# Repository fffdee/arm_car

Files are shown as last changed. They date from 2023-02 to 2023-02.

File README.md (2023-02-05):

# arm_car铁甲虫遥控小车

### 关于模型（model）

#### 1.除了电机，轴承还有轮子不用打印，其他都可以用3d打印。

#### 2.准备标准件：轴承（10mm*3mm）x4，螺钉（20mm以上*3mm）x4，舵机x2，N20电机（长轴:大于12mm）x2，N20电机轮子x2

### 关于软件（software）

#### 1.只需要修改wifi或者手机热点的名称和密码即可

### 关于硬件（hardware）

#### geber 文件夹下是打板文件

#### BOM 文件夹下是零件清单（SMT用）

#### pick 文件下是坐标文件（SMT用）

### 关于APP

#### 打开后输入192.168.190.125（小车ip，可以在软件中修改）就可开始控制小车了（保证小车已经连上wifi或者手机热点）

#### 视频详情链接：【【开源】寒假在家无聊，做了一个甲虫车】 https://www.bilibili.com/video/BV1HY411D7DA/?share_source=copy_web&vd_source=6f5872d400f2b982828888d93e5dddf6

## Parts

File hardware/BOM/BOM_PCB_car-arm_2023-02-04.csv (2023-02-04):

ID | Name | Designator | Footprint | Quantity | Manufacturer Part | Manufacturer | Supplier | Supplier Part | Price
1 | LESD8D3.3CAT5G | D3,D4 | SOD-882_L1.0-W0.6-BI | 2 | LESD8D3.3CAT5G | LRC(乐山无线电) | LCSC | C172409 | 0.0894
2 | HDR-M-2.54_1x2 | J5,J6,J1 | HDR-M-2.54_1X2 | 3 |  |  | LCSC | C124375 | 0.1611
3 | 10u | C1,C2,C6,C12,C13,C14,C18,C22 | C0402 | 8
4 | 0.1u | C3,C4,C5,C8,C9,C10,C11,C17,C20,C21,C26 | C0402 | 11
5 | 22pf | C7 | C0402 | 1
6 | 10U | C15,C16 | C0402 | 2
7 | 1u | C19 | C0402 | 1
8 | LESD5D5.0CT1G | D2 | SOD-523_L1.2-W0.8-LS1.6-BI | 1 | LESD5D5.0CT1G | LRC(乐山无线电) | LCSC | C383211 | 0.1559
9 | SS-12D00-G4 | NO-> | SS-12D00-G4 | 1
10 | HDR-M-2.54_1x3 | J2,J3,J4 | HDR-M-2.54_1X3 | 3 |  |  | LCSC | C180248 | 1.2443
11 | 2.2uH | L6 | IND-SMD_L3.5-W3.0 | 1 | SMTDR32-2R2M | 3L COILS | LCSC | C326182 | 0.6574
12 | LED-0603_G | LED4 | LED0603_GREEN | 1 | 19-217/GHC-YR1S2/3T | EVERLIGHT(台湾亿光) | LCSC | C72043 | 0.1678
13 | LED-0603_R | LED5 | LED0603_RED | 1 | 19-217/R6C-AL1M2VY/3T | EVERLIGHT(台湾亿光) | LCSC | C72044 | 0.1041
14 | AO3401A | Q1 | SOT-23_L2.9-W1.3-P1.90-LS2.4-BR | 1 | AO3401A | AOS | LCSC | C15127 | 0.5469
15 | S8050 | Q2,Q3 | SOT-23(SOT-23-3) | 2 | S8050 | Yenji | LCSC | C364312 | 0.0687
16 | 100k | R1,R2,R5,R8 | R0402 | 4
17 | 1k | R6,R7,R9,R10 | R0402 | 4
18 | 10k | R18,R19,R23,R24,R25,R26,R27,R47 | R0402 | 8
19 | 1.2K | R28 | R0402 | 1
20 | 0 | R29 | R0402 | 1
21 | 580k | R48 | R0402 | 1
22 | 150k | R49 | R0402 | 1
23 | sw1 | SW1,SW2 | 3*4龟仔按键 | 2 | TS-1101-C-W | XKB Connectivity(中国星坤) | LCSC | C318938 | 0.2205
24 | RZ7888 | U1,U2 | SOP-8_L4.9-W3.9-P1.27-LS6.0-BL | 2 | RZ7888 | RZ | LCSC | C94177 | 2.1132
25 | SY8088AAC | U3 | SOT-23-5_L3.0-W1.7-P0.95-LS2.8-BR | 1 | SY8088AAC | Silergy | LCSC | C79313 | 0.5151
26 | ME6211C33M5G | U4 | SOT-23-5_L3.0-W1.7-P0.95-LS2.8-BR | 1 | ME6211C28M5G-N | MICRONE(南京微盟) | LCSC | C53099 | 0.4775
27 | W2812B | U5,U6,U7,U8 | LED-SMD_4P-L5.0-W5.0-LS5.4-TL | 4 | W2812B | null | LCSC | C2935753
28 | TP4056 | U11 | ESOP-8_L4.9-W3.9-P1.27-LS6.0-BL-EP | 1 | TP4056 | TOPPOWER | LCSC | C16581 | 1.2281
29 | ESP-12F(ESP8266MOD) | U12 | WIFIM-SMD_ESP-12F-ESP8266MOD | 1 | ESP-12F(ESP8266MOD) | Ai-Thinker | LCSC | C82891 | 13.51
30 | CH340C | U13 | SOP-16_150MIL | 1 | CH340C | WCH | LCSC | C84681 | 3.01
31 | TYPEC-304J-BCP16 | USB1 | USB-C-SMD_TYPEC-304J-BCP16 | 1 | TYPEC-304J-BCP16 | XUNPU(讯普) | LCSC | C2835315 | 2.25

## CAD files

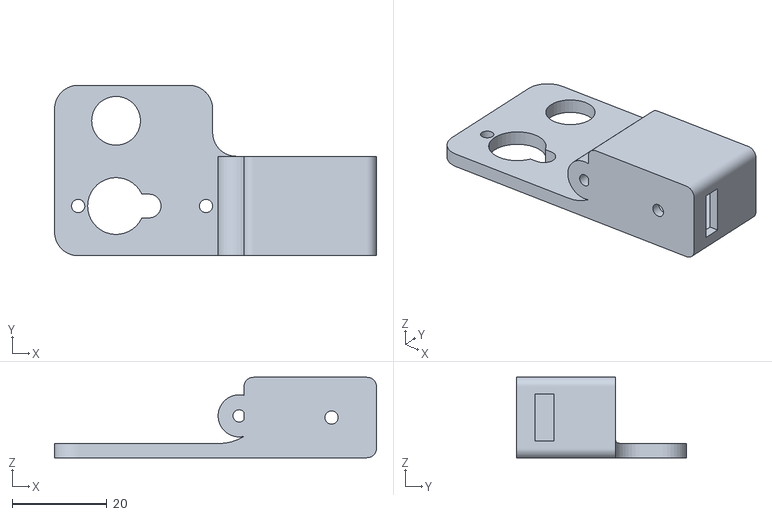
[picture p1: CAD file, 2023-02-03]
model/STL/动力臂.STL
68.0 x 36.0 x 17.0

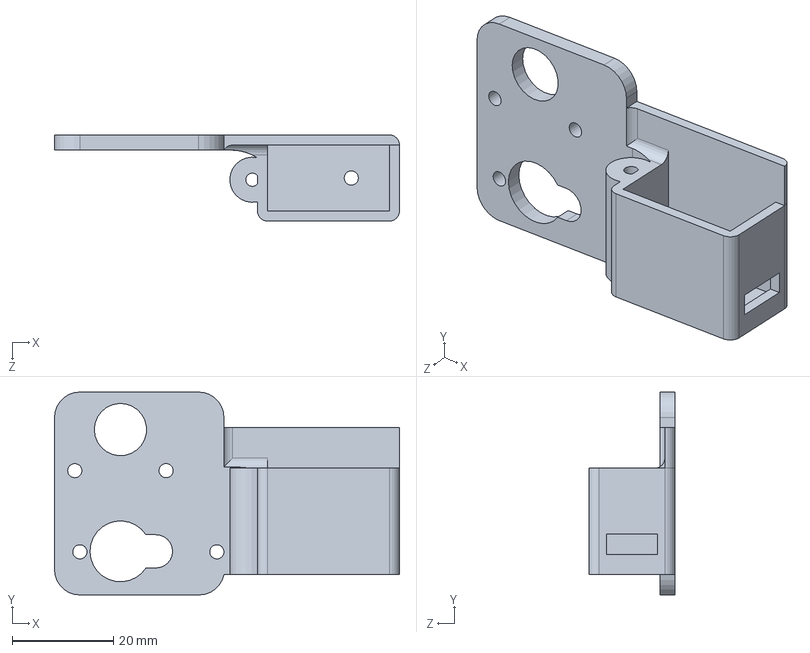
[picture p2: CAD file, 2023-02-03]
model/云台.SLDPRT
68.0 x 40.0 x 17.0 mm

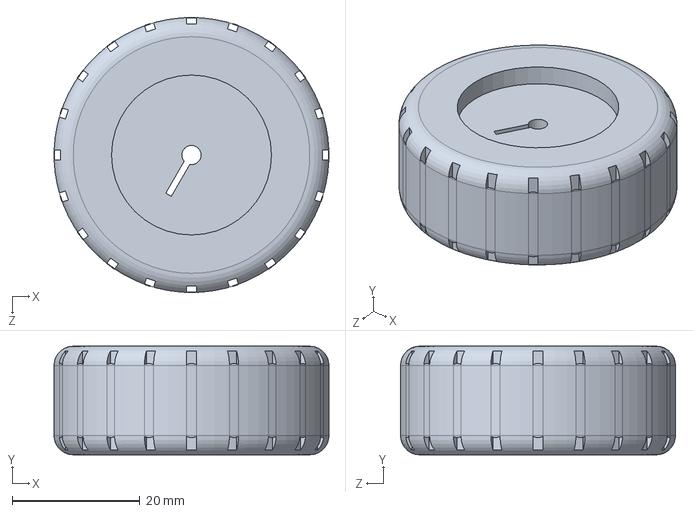
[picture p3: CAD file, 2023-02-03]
model/轮子.SLDPRT
43.0 x 17.0 x 43.0 mm

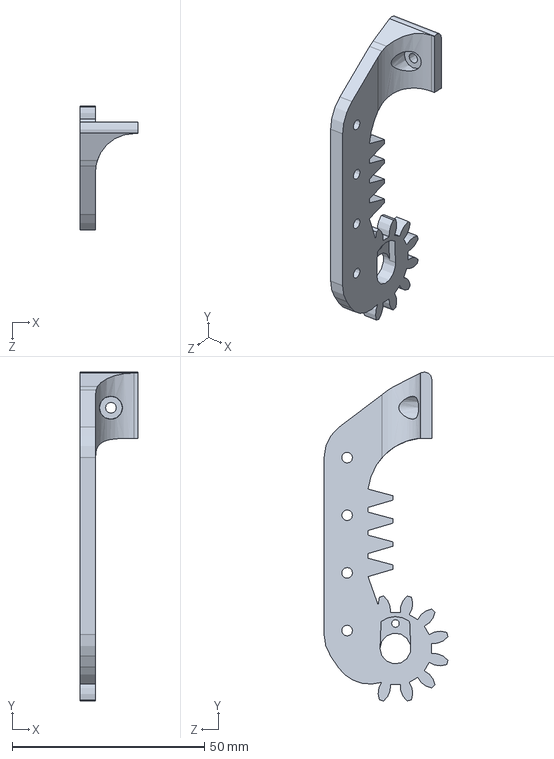
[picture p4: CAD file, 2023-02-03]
model/动力齿轮.SLDPRT
15.0 x 85.6 x 32.2 mm

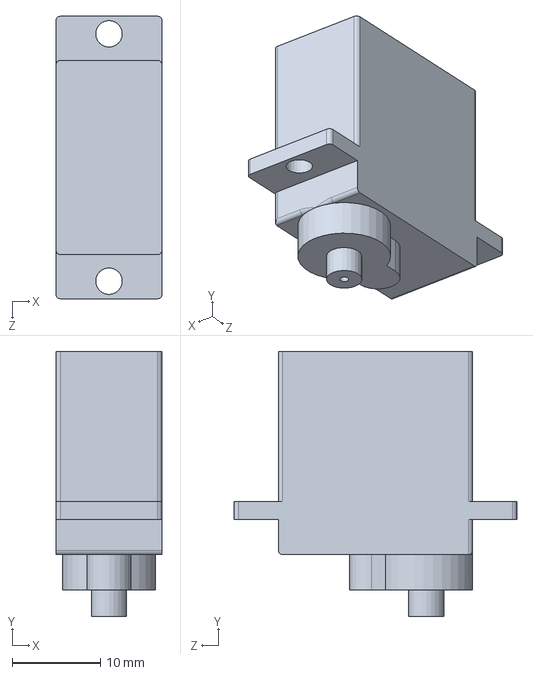
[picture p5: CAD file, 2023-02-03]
model/蓝色小舵机.SLDPRT
12.0 x 30.0 x 32.0 mm

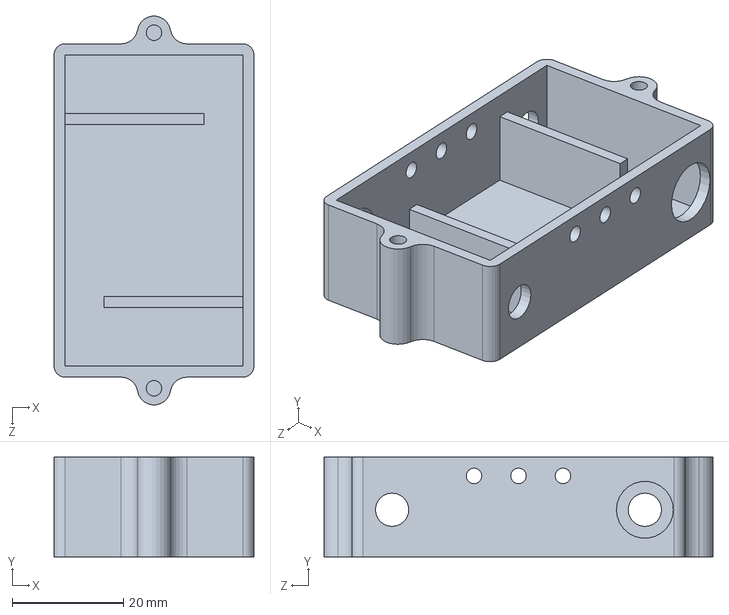
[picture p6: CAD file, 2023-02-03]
model/底盘.SLDPRT
36.0 x 18.0 x 70.0 mm

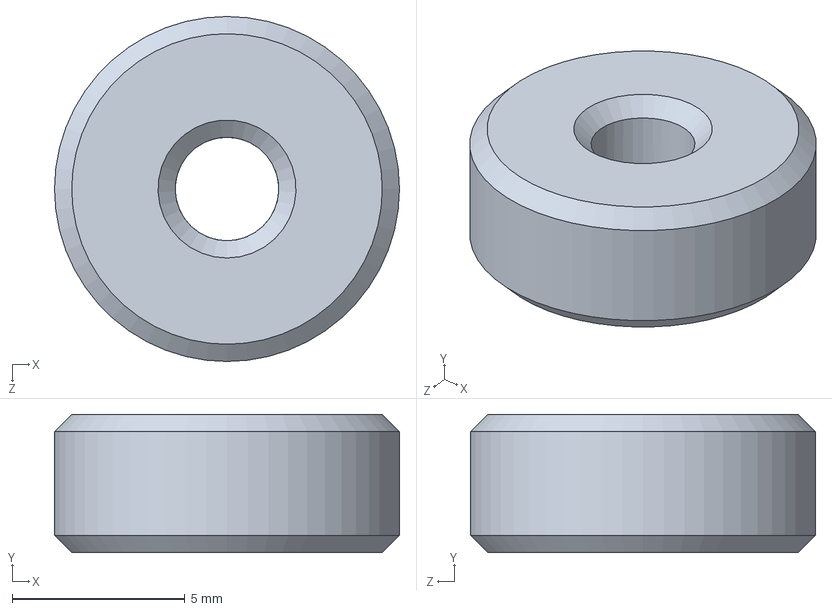
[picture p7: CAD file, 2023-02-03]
model/轴承.SLDPRT
10.0 x 4.00 x 10.0 mm

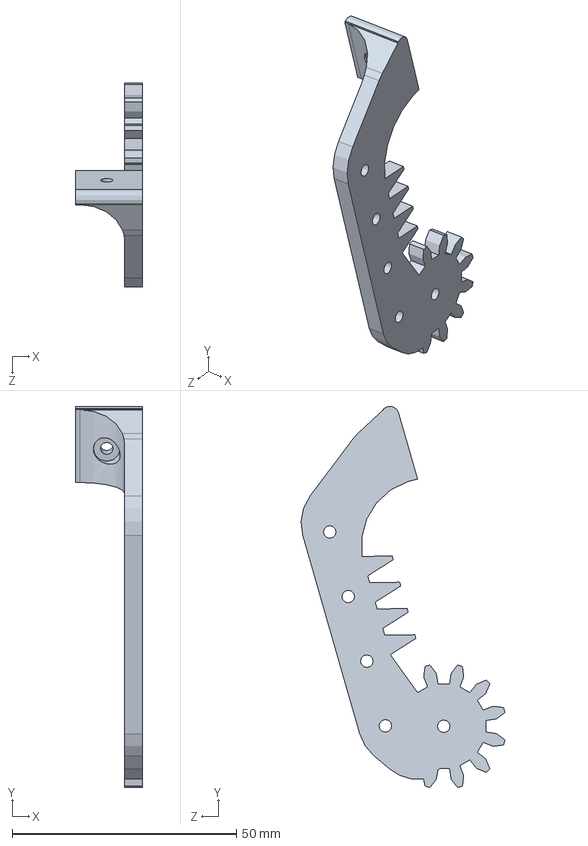
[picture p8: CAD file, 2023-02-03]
model/辅助齿轮齿轮.SLDPRT
15.0 x 85.0 x 45.5 mm

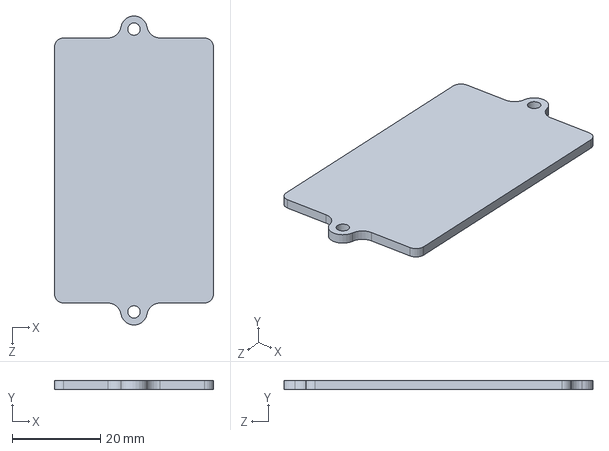
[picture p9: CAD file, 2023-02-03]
model/盖板.SLDPRT
36.0 x 2.00 x 70.0 mm

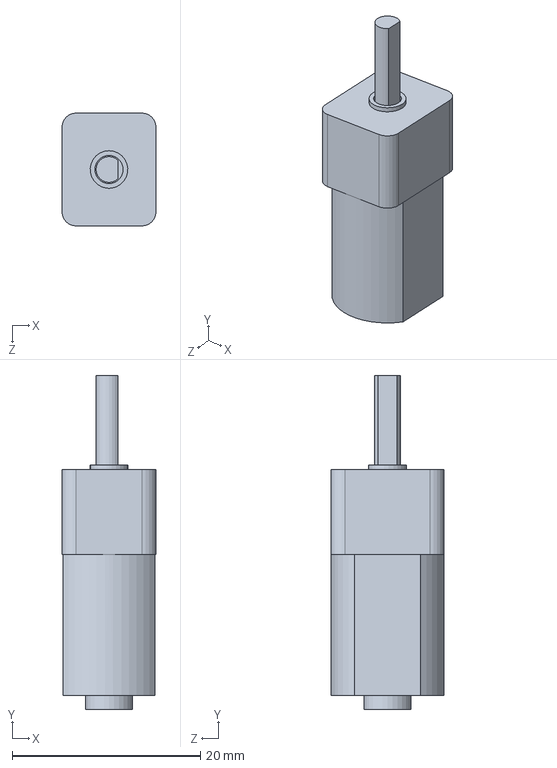
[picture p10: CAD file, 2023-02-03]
model/N20电机.SLDPRT
10.0 x 35.5 x 12.0 mm

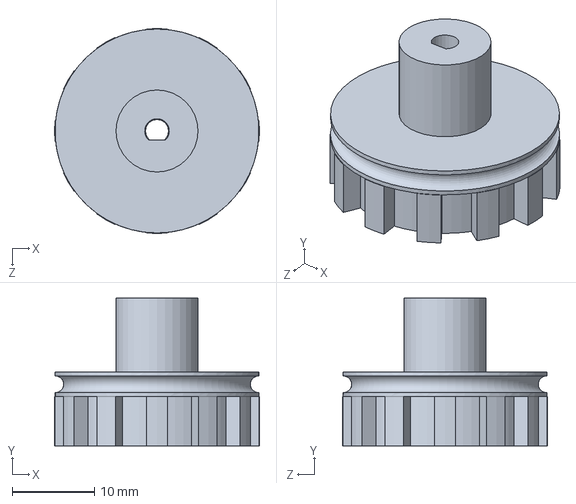
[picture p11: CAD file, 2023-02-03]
model/轮子连接器.SLDPRT
25.0 x 18.0 x 25.0 mm

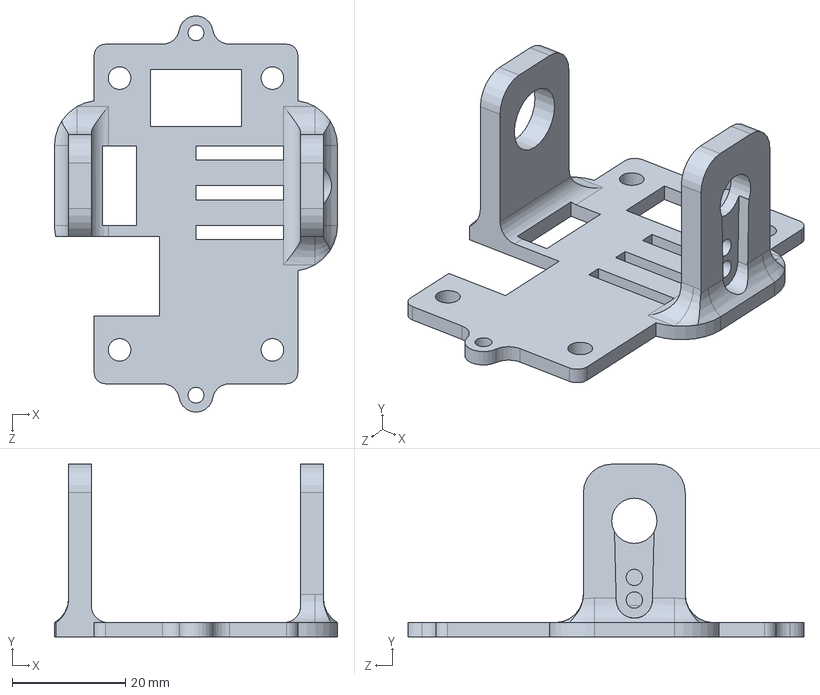
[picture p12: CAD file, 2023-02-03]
model/盖板舵机台.SLDPRT
50.0 x 30.5 x 70.0 mm

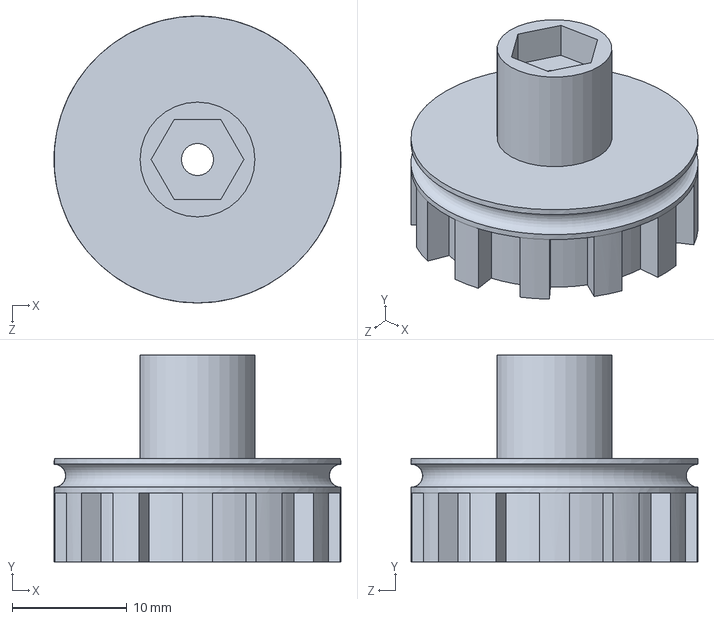
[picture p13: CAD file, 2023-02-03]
model/从动连接器 .SLDPRT
25.0 x 18.0 x 25.0 mm

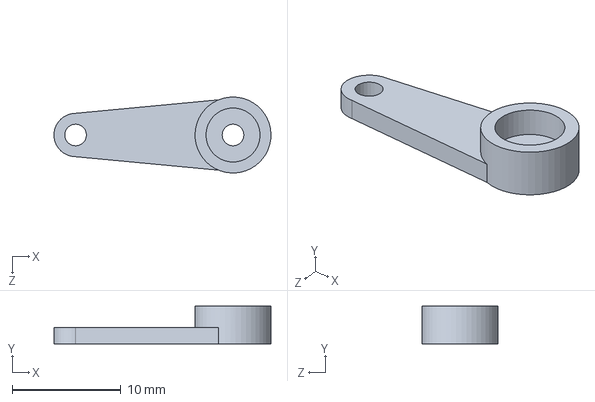
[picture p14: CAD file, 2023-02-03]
model/舵机柄.SLDPRT
20.0 x 3.50 x 7.00 mm

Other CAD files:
model/电池.SLDPRT
model/STL/云台.STL
model/STL/从动连接器 .STL
model/STL/动力齿轮.STL
model/STL/底盘.STL
model/STL/盖板舵机台.STL
model/STL/轮子连接器.STL
model/STL/辅助齿轮齿轮.STL

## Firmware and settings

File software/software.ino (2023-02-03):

 #include <ESP8266WiFi.h>
#include <ESP8266WiFiMulti.h>   // 使用WiFiMulti库 
#include <ESP8266WebServer.h>   // 使用WebServer库
#include <Servo.h> 
#include <EEPROM.h>
#include "StringSplitter.h"
#include <WiFiUdp.h>
#include <Adafruit_NeoPixel.h>

Servo myServo2;
Servo myServo1;

Adafruit_NeoPixel pixels(4, 5, NEO_GRB + NEO_KHZ800);


ESP8266WiFiMulti wifiMulti;     // 建立ESP8266WiFiMulti对象,对象名称是 'wifiMulti'
 
ESP8266WebServer server(80);    // 建立网络服务器对象，该对象用于响应HTTP请求。监听端口（80）
 
IPAddress local_IP(192, 168, 190, 125); // 设置开发板联网后的IP（这个就是填到app里面的IP地址）
IPAddress gateway(192, 168, 190, 1);    // 设置网关IP（通常网关IP是手机的IP）（开热点给开发板连的手机）
IPAddress subnet(255, 255, 255, 0);   // 设置子网掩码
IPAddress dns(192,168,190,1);           // 设置局域网DNS的IP（通常局域网DNS的IP是手机的IP）（开热点给开发板连的手机）

int servo1Value=90;
int servo2Value=90;

int speedValue=200;
int anglexValue = 90;
int angleyValue = 90;
void setup(void){
  
  Serial.begin(115200);          // 启动串口通讯
  EEPROM.begin(25);
  myServo2.attach(12); //设置引脚2为舵机引脚
  myServo1.attach(14);  
  myServo1.write(anglexValue);
  myServo2.write(angleyValue);
  pinMode(13,OUTPUT);
  pinMode(16,OUTPUT);
  pinMode(0,OUTPUT);
  pinMode(4,OUTPUT);
  // 设置开发板网络环境
  if (!WiFi.config(local_IP, gateway, subnet)) {

  } 
  
  wifiMulti.addAP("BanGO", "88888888"); // 将需要连接的一系列WiFi ID和密码输入这里
  wifiMulti.addAP("ssid_from_AP_2", "your_password_for_AP_2"); // ESP8266-NodeMCU再启动后会扫描当前网络
  wifiMulti.addAP("ssid_from_AP_3", "your_password_for_AP_3"); // 环境查找是否有这里列出的WiFi ID。如果有
                            // 则尝试使用此处存储的密码进行连接。
  
  // 尝试进行wifi连接。
  while (wifiMulti.run() != WL_CONNECTED) { 
    delay(250);

  }
 

 
  server.on("/control", handleUpdate);        // 处理服务器更新函数
  server.on("/arm", arm);        // 处理服务器更新函数
  server.on("/hand", hand);        // 处理服务器更新函数
  server.on("/speed", Setspeed);
  server.begin();                            // 启动网站服务

  pixels.begin(); 
  pixels.clear();

  pixels.setPixelColor(0, pixels.Color(10,10,10));
  pixels.setPixelColor(1, pixels.Color(10,10,10));
  pixels.setPixelColor(2, pixels.Color(10,10,10));
  pixels.setPixelColor(3, pixels.Color(10,10,10));
  pixels.show();   // Send the updated pixel colors to the hardware.
  delay(1000);
  pixels.setPixelColor(0, pixels.Color(0,0,0));
  pixels.setPixelColor(1, pixels.Color(0,0,0));
  pixels.setPixelColor(2, pixels.Color(0,0,0));
  pixels.setPixelColor(3, pixels.Color(0,0,0));
  pixels.show();   // Send the updated pixel colors to the hardware.
  delay(1000);
}
 
void loop(void){
  server.handleClient(); // 检查http服务器访问


  delay(100);
}



//重点改这里就好了 
void arm(){
   anglexValue = server.arg("anglex").toInt(); 
   myServo1.write(anglexValue); 
   Serial.print("anglexValue = ");  Serial.println(anglexValue);
}

void hand(){
   angleyValue = server.arg("angley").toInt(); 
   myServo2.write(angleyValue); 
   Serial.print("angleyValue = ");  Serial.println(angleyValue);
}

void Setspeed(){
   speedValue = server.arg("speed").toInt(); 
  
   Serial.print("speedValue = ");  Serial.println(speedValue);
}

void handleUpdate(){
        // 获取客户端发送HTTP信息中的整数数值
  int leftupValue = server.arg("leftup").toInt();  // 获取客户端发送HTTP信息中的按键控制量
  int leftdownValue = server.arg("leftdown").toInt(); 
  int rightupValue = server.arg("right").toInt();
  int rightdownValue = server.arg("rightdown").toInt();
  int stopValue = server.arg("stop").toInt();              

 

  if(leftupValue == 1){
    analogWrite(0,speedValue);
    analogWrite(4,0);
   
    pixels.setPixelColor(0, pixels.Color(10,10,150));
    pixels.setPixelColor(1, pixels.Color(10,10,150));
    pixels.setPixelColor(2, pixels.Color(10,10,150));
    pixels.setPixelColor(3, pixels.Color(10,10,150));
    pixels.show();   // Send the updated pixel colors to the hardware.
 
   }

  if(leftdownValue == 1){

    analogWrite(0,0);
    analogWrite(4,speedValue);
    pixels.setPixelColor(0, pixels.Color(10,150,10));
    pixels.setPixelColor(1, pixels.Color(10,150,10));
    pixels.setPixelColor(2, pixels.Color(10,150,10));
    pixels.setPixelColor(3, pixels.Color(10,150,10));
    pixels.show();   // Send the updated pixel colors to the hardware.
  
  }
  if(stopValue == 1){
    analogWrite(13,0);
    analogWrite(16,0);
    analogWrite(0,0);
    analogWrite(4,0);
    pixels.setPixelColor(0, pixels.Color(0,0,0));
    pixels.setPixelColor(1, pixels.Color(0,0,0));
    pixels.setPixelColor(2, pixels.Color(0,0,0));
    pixels.setPixelColor(3, pixels.Color(0,0,0));
    pixels.show();   // Send the updated pixel colors to the hardware.
   
   
  
  }

  if(rightupValue == 1){
    analogWrite(16,0);
    analogWrite(13,speedValue);
    pixels.setPixelColor(0, pixels.Color(150,10,10));
    pixels.setPixelColor(1, pixels.Color(150,10,10));
    pixels.setPixelColor(2, pixels.Color(150,10,10));
    pixels.setPixelColor(3, pixels.Color(150,10,10));
    pixels.show();   // Send the updated pixel colors to the hardware.
  
  }

  if(rightdownValue == 1){
    analogWrite(16,speedValue);
    analogWrite(13,0);
   
    pixels.setPixelColor(0, pixels.Color(0,150,150));
    pixels.setPixelColor(1, pixels.Color(0,150,150));
    pixels.setPixelColor(2, pixels.Color(0,150,150));
    pixels.setPixelColor(3, pixels.Color(0,150,150));
    pixels.show();   // Send the updated pixel colors to the hardware.
  }
  
   server.send(200, "text/plain", "Received"); // 发送http响应
  // 通过串口监视器输出获取到的变量数值
  Serial.print("stopValue = ");  Serial.println(stopValue);  
  Serial.print("rightdownValue = ");  Serial.println(rightdownValue); 
  Serial.print("leftupValue = ");  Serial.println(leftupValue); 
  Serial.print("leftdownValue = ");  Serial.println(leftdownValue);
  Serial.print("rightupValue = ");  Serial.println(rightupValue);       
 Serial.print("speedValue = ");  Serial.println(speedValue);
  Serial.println("=================");    
}
